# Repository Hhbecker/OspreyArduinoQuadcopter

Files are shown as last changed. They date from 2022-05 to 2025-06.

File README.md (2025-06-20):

<h1 align="center">
The Osprey Drone Mark I with Osprey Flight Controller Version 1.0
</h1>

<p align="center">
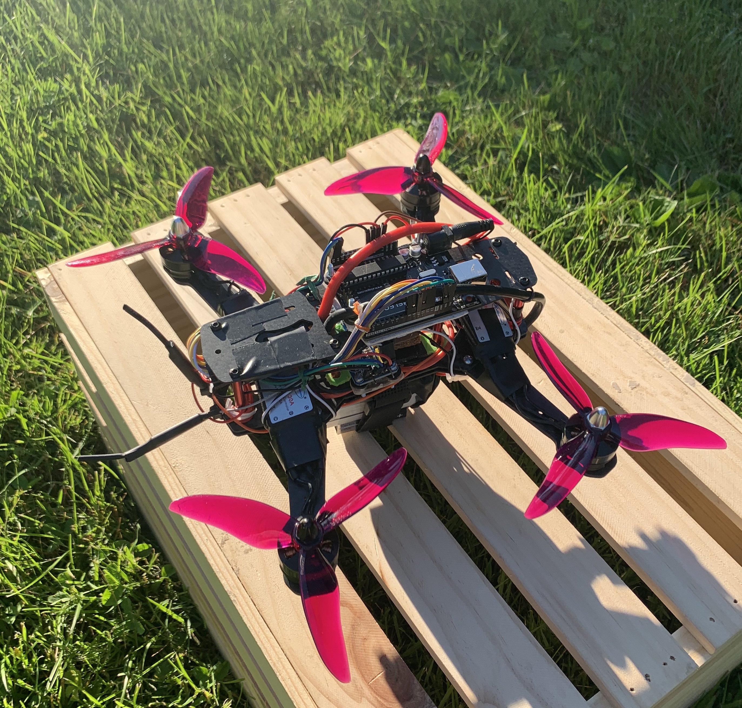
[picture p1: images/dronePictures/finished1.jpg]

</p>

<h5 align="center">
An Arduino based quadcopter build with personally developed flight control software
</h5>

### Features:
* Automated PID stabilization for roll pitch and yaw axes 
* Joystick control of roll pitch and yaw axes 
* Joystick throttle mapped directly to motor power
* Approximately 20Hz flight controller refresh rate

### Why Drones?
I see drones as the perfect engineering challenge because they require knowledge from a range of disciplines including physics, electrical engineering, computer science, and math. 
This drone project has also provided me with experience 1. developing embedded software for a real-time application, 2. designing and constructing circuits and electrical hardware, and 3. implementing an algorithm based on control theory mathematics. Not only are drones a great engineering challenge but they also have innumerous real world applications including in disaster relief, law enforcement, agriculture, and war. 

### Circuit Diagram
<p align="center">

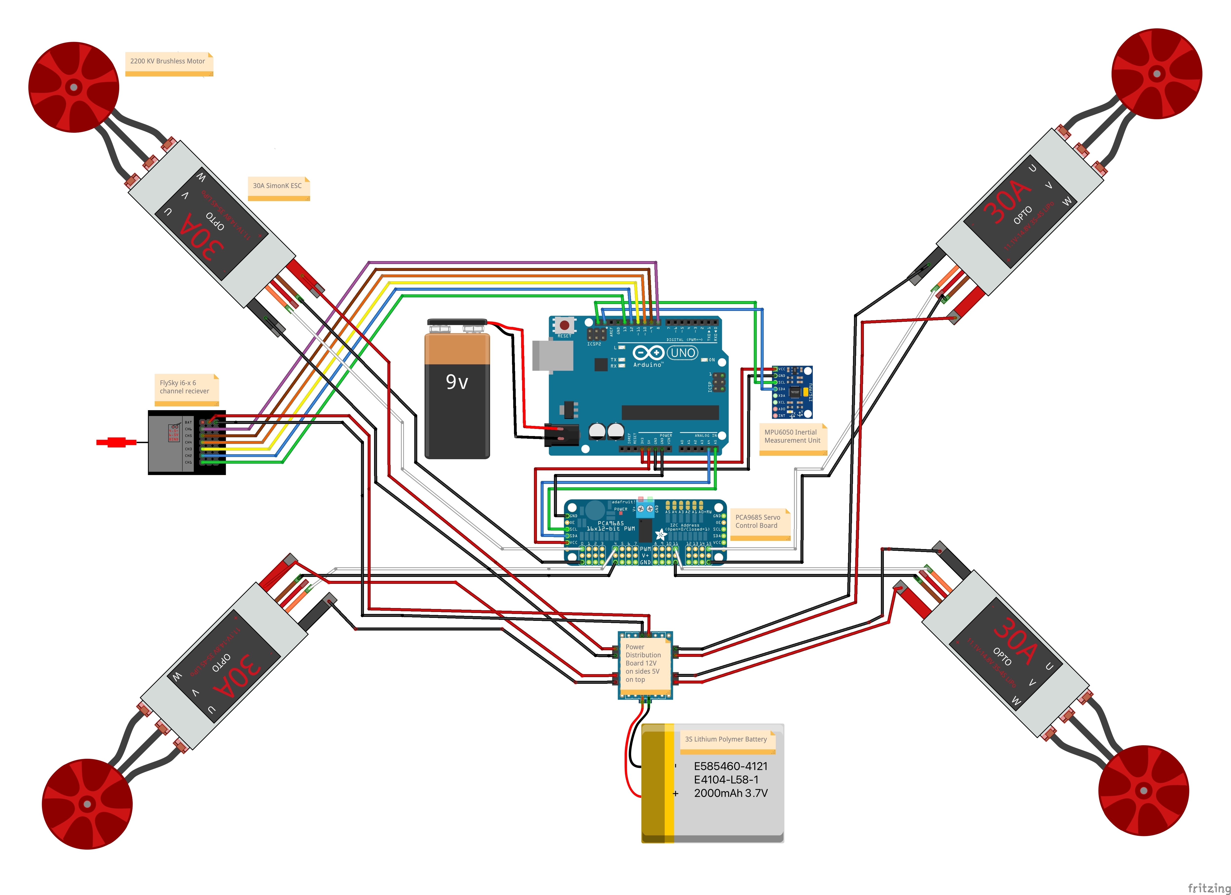
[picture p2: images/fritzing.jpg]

</p>

### The Basics of Quadcopter Flight
A drone has three axes of rotation: roll, pitch, and yaw. The primary goal of the Osprey Flight Controller V1.0 is to maintain stability in flight by continously adjusting the speed of each individual motor in order to abruptly and accurately correct any unwanted rotation about each of the three axes. The different colored rotors in the image below represent the front and rear rotors of the drone. It is important to mention that diagonal rotors spin in the same direction whereas adjacent motors spin in the opposite direction in order to balance the motor torques.

<p align="center">
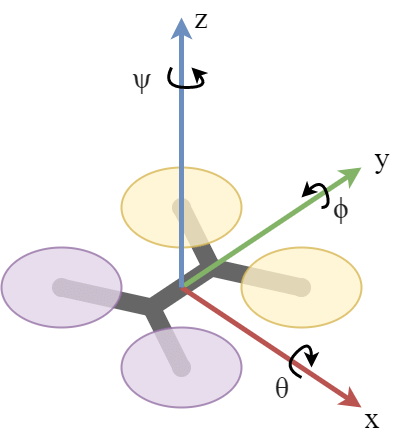
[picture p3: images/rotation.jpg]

</p>

<p align="center">
<b>Vizualization of the three axes of rotation. Y = roll, X = pitch, and Z = yaw.</b>
</p>

The onboard accelerometer and gyroscope are used to calculate the rotation of the drone along these three axes in real time. The observed rotation is fed into the flight control algorithm to calculate the new motor speeds necessary to correct for any unwanted rotation. The flight control algorithm runs in a loop continously making these corrections and adjustments throughout the duration of the flight. The stability of the drone is ultimately a function of how quickly corrections are calculated and implemented by the motors. Each component on the drone plays a role in accomplishing this task.

### Software Architecture 
The arduino runs a continuous loop with the same set of functions called each time the loop executes. The diagram below shows the main loop functions in the order of their execution. This code is pulled directly from the main loop of the Osprey Flight Controller V1.0.

<p align="center">
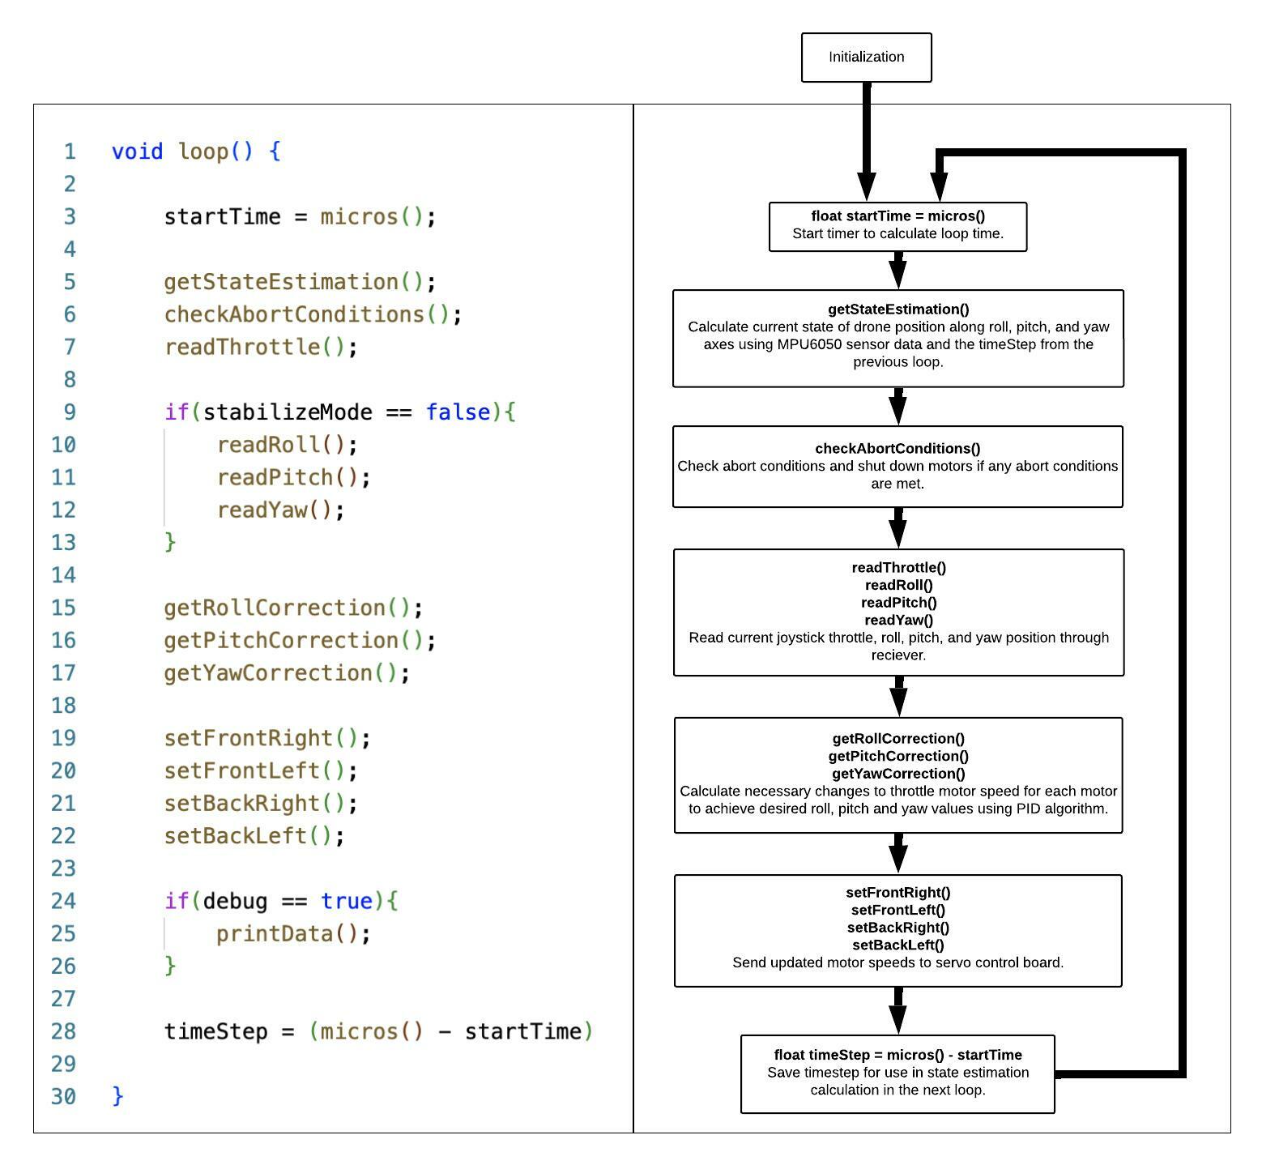
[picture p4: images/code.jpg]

</p>

### The Control Algorithm
Control theory is a branch of applied mathematics that deals with the use of feedback to influence the behaviour of a system in order to achieve a desired goal. In the case of drone flight, the current rotation about each axis must be "fed-back" into the control algorithm and used to determine how much the motor speeds should change to achieve the desired rotation set by the joysticks.

The method of feedback control used in the Osprey Flight Controller is known as PID Control. PID control is one of the most common control algorithms used in industry because it is simple to understand and implement yet still provides robust performance. PID algorithms consist of three basic coefficients; proportional, integral and derivative. These coefficients are scaled or "tuned" to get the optimal response. 

To better understand PID control let's use the roll axis of the Osprey drone as an example. As previously discussed, the flight controller calculates the drone's attitude about the roll axis and compares the current rotation to the desired rotation set by the joystick. Let's say the desired roll is 0º, but a gust of wind induces a roll of 30º. The error term (the difference between the current and desired rotation) is now 30º.

<p align="center">
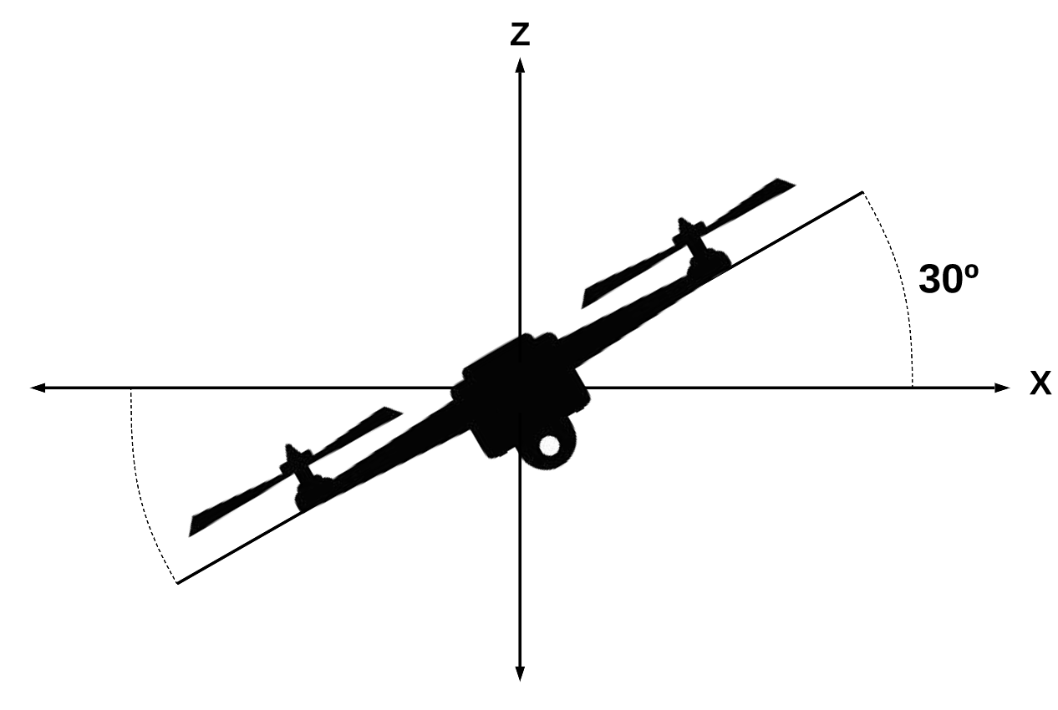
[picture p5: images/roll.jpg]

</p>

<p align="center">
<b>Drone rolling 30º with a setpoint of 0º resulting in a roll error term of 30.</b>
</p>

This error term is then passed into the PID controller. Inside the PID controller a proportional, integral, and derivative response to this error term are calculated separately and finally summed together. The sum of the proportional, integral, and derivative response to the error term is the output of the controller which is combined with the throttle value to calculate the new motor speeds. Notice the gain term (Kp for proportional, Ki for integral, and Kd for derivative) in front of each PID path in the diagram below. This gain is adjusted to increase or decrease the effect of the given term on the overall controller output. The PID tuning process is necessary to find the optimal response and robustness for a particular system. 

<p align="center">
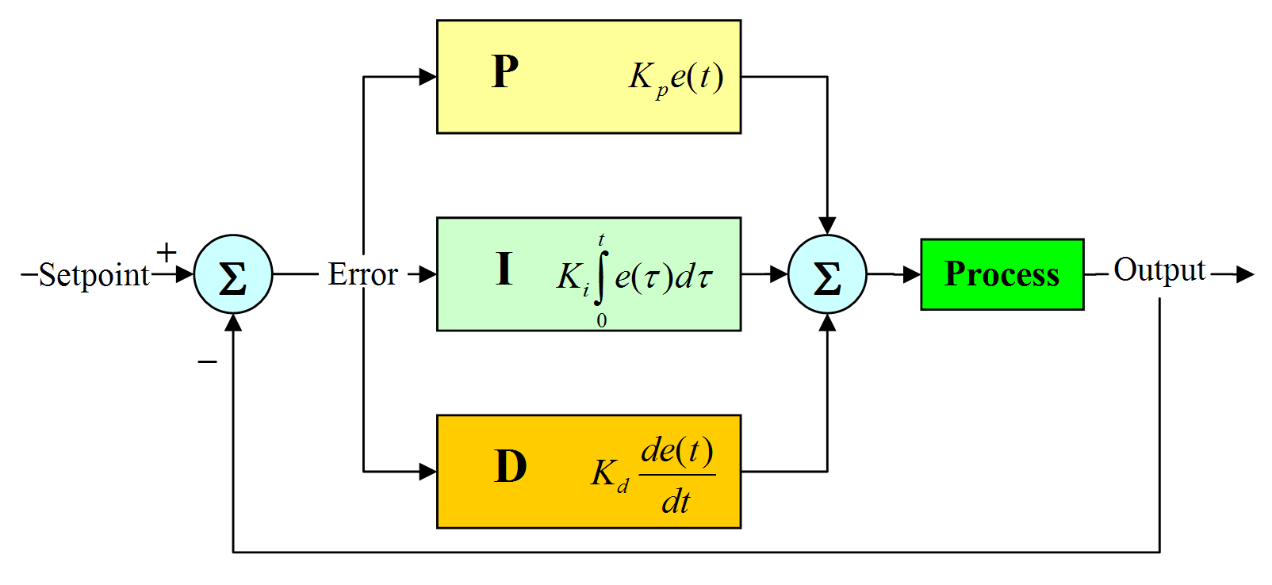
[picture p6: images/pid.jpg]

</p>

<p align="center">
<b>The structure of a PID controller showing the error term passed through the proportional, integral, and derivative paths.</b>
</p>

Because the drone is rolling to the left in our example we would expect our PID controller to reduce the power to the motors on the right and increase the power to the motors on the left. How do the proportional, integral, and derivative terms each respond to the error to affect the controller output?

#### Proportional term
As you might expect, the proportional term grows proportionally with the size of the error term. A larger error will result in a larger absolute contribution from the proportional term to the controller output. 

#### Integral term
The integral term is the integration of the error over time. With every execution of the loop, the current error is added to the sum of all past errors. The integral term is necessary to overcome what is known as steady state error. Steady state error occurs when an equilibrium is reached with the proportional term and an opposing force at a state of nonzero error. This often happens when the error term is small, because the proportional term will also be small and may be too small to compensate for the error. The integral term accumulates this residual error over time to drive the system toward its commanded value. Integral terms are tuned to be inconsequential in the transient response  and only become significant over time. Integral windup occurs when the integral term saturates the motor's capabilities and must be considered when designing a PID controller. A simple strategy to avoid integral windup is to cap the integral term at a predetermined value.

#### Derivative term
The derivative term takes into account the rate of change of the error term. The derivative term is sometimes called the damping term because its primary responsibility is to prevent the system from overcorrecting due to the contribution of the proportional term. The derivative term is constrained by its tendency to amplify sensor noise. If the derivative gain is too high, the system will lose stability because the derivative term's response to sensor noise  will exert an oversized affect on the controller output.

In summary, the basic idea behind a PID controller is to 1. Read a sensor, 2. Compute the difference between the sensor reading and the desired setpoint (the error term), and 3. Compute the desired change in motor power by summing a proportional, integral, and derivative response to the error term. 

#### PID Tuning
A flawless flight controller still will not fly without reasonable gains. Testing the overall function of the drone and tuning the gains in a safe and controlled environment before attempting to fly is the smart approach to drone development (I learned the hard way). To safely tune the gains I built a simple test rig shown below. The roll, pitch, and yaw axes must be tested and tuned individually. For each axis, the center of rotation on the test rig should be located directly through the center of gravity of the drone to best simulate flight. Make sure to balance weight, motor thrusts, and motor torques along each axis so the drone remains level on the test rig in the absence of perturbations before testing the PID controller.

<br/>

<p align="center">
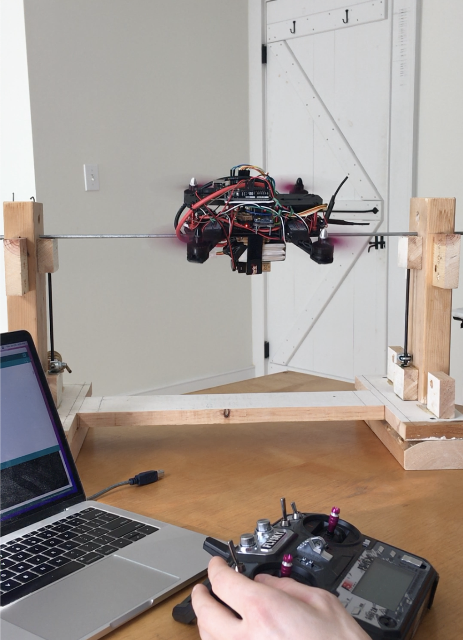
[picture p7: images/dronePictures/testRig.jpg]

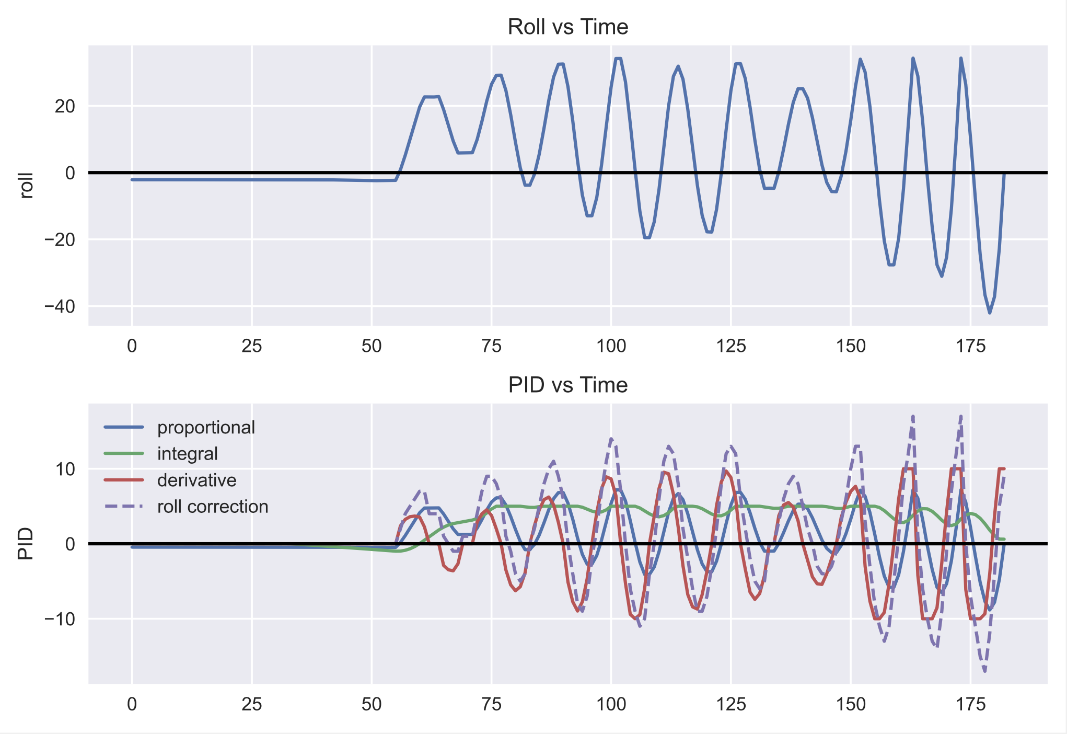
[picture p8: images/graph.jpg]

</p>

<p align="center">
<b>Left: handmade roll and pitch test rig. Right: graph of PID output during roll test.</b>
</p>

#### The Ziegler Nichols PID Tuning Method
1. Set integral and derivative gains to zero
2. Tune the proportional gain to achieve even, steady oscillations when perturbed. 
4. Add the derivative term and tune the gain to remove overshoot. 
5. Add the integral term and tune the gain to compensate for any steady state error.

### State Estimation 
The Osprey Flight Controller incorporates gyroscope and accelerometer data from the MPU6050 inertial measurement unit to achieve a 3 degrees of freedom attitude estimation about the roll, pitch, and yaw axes. The MPU6050 is a low budget, low power, 6-axis microelectromechanical inertial measurement unit that can easily interface with Arduino using the I2C protocol. 

<p align="center">
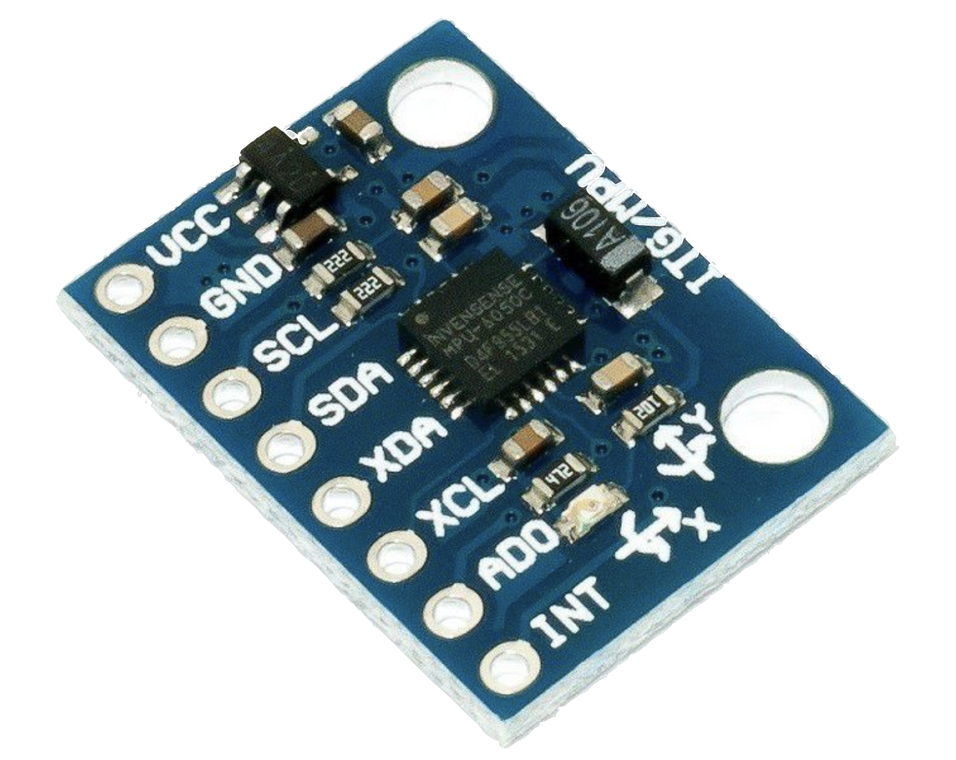
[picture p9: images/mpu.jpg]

</p>
<p align="center">
<b>An MPU6050 inertial measurement unit.</b>
</p>

The MPU6050 gyroscope measures angular rate. The angular rate is integrated with respect to time to get an estimate of the current position. Obviously, the smaller the timestep of the integration, the more accurate the angular position estimate will be. This method can be used to calculate roll, pitch, and yaw angular position estimates and is very accurate in flight. 

The MPU6050 accelerometer measures linear acceleration along the X, Y, and Z axes. The angular position is calculated from each accelerometer linear acceleration reading using Euler angle based trigonometry. Only roll and pitch can be calculated with this method. This calculation relies on the drone being in an inertial reference frame, where the accelerometer registers 1g. During accelerating flight, these calculations become inaccurate. At rest the accelerometer based estimations will recenter any gyroscope drift. Kornelius Jarzębski's MPU6050 library was used to calculate the accelerometer based angular position estimates and these estimates were fused with the gyroscope estimates using a low pass filter for the accelerometer based state estimation and a high pass filter for the gyroscope based state estimation. This filtering strategy is used because the accelerometer based estimations are susceptible to large amounts of error in the short term but do not drift in the long term, whereas the gyroscope based estimations are very accurate in the short term but will drift over time as small errors accumulate.

### Flight Controller Timing
Flight controller speed is crucial for drone stability. A slower flight controller loop time negatively affects stability because it decreases the accuracy of the state estimation and also does not give the motors as much time to adjust their speed. The Osprey Flight Controller relies on several different hardware components as well as software to do its job. It's important to understand the time it takes to complete each part of the loop, so that optimization efforts can focus on the biggest bottlenecks. The default operating frequency for Arduino Uno R3 is 16MHz. The average timestep (total loop time) of the Osprey Flight Controlller V1.0 is approximately 20Hz in Stabilize Mode. This is unfortunately far too slow to allow for the stability required to film or maneuver. Modern F4 flight controllers allow for incredibly smooth and aggresssive flight with loop times of 32KHz which is three orders of magnitude faster than the Osprey Flight Controller V1.0. 

The MPU6050 has a maximum sample rate north of 1Hz but in this project the MPU6050 is only sampled once every loop. The timestep is often kept constant when integrating sensor data with respect to time. I chose to vary the time step to avoid using the delay() function which is a blocking function and slowed the overall loop time too much. The best solution would be to handle integration of the sensor data on a separate microcontroller to allow for a constant timestep without slowing down other flight controller tasks. 

The internal clock of the servo control board can be set to operate at a frequency of up to 1526Hz. I set the frequency to 400Hz for communication with the SimonK ESCs. The SimonK ESCs are capabale of a 400Hz refresh rate. The motors are lower end but are still capable of accelerating and decellerating quickly enough.

### Construction Process
<p align="center">
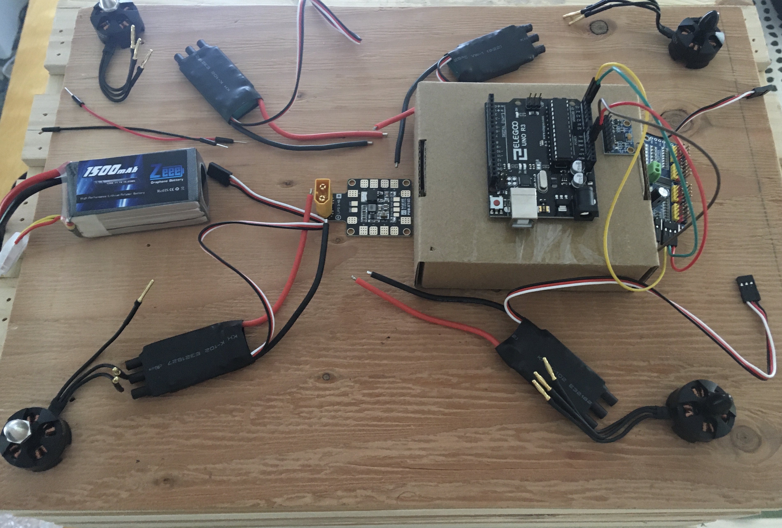
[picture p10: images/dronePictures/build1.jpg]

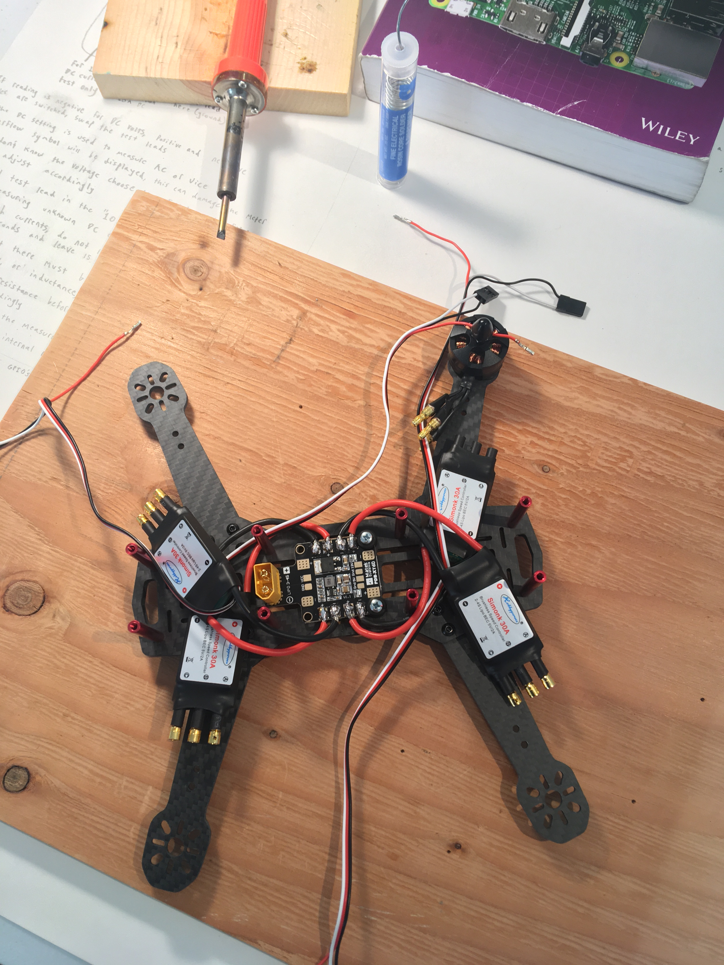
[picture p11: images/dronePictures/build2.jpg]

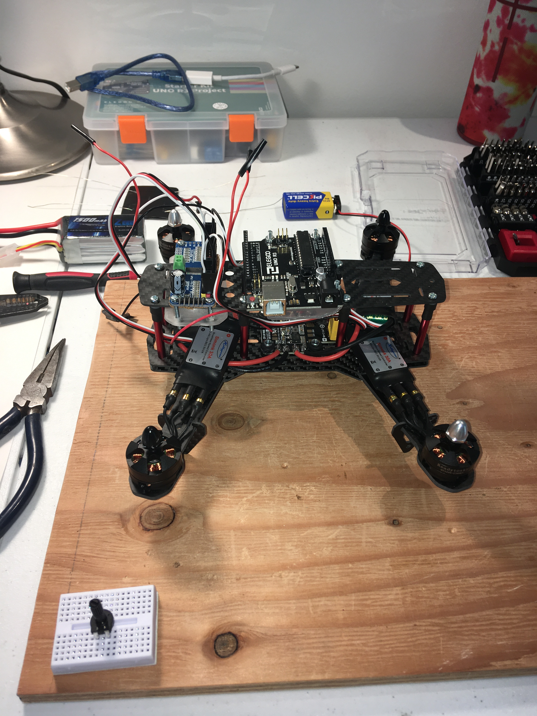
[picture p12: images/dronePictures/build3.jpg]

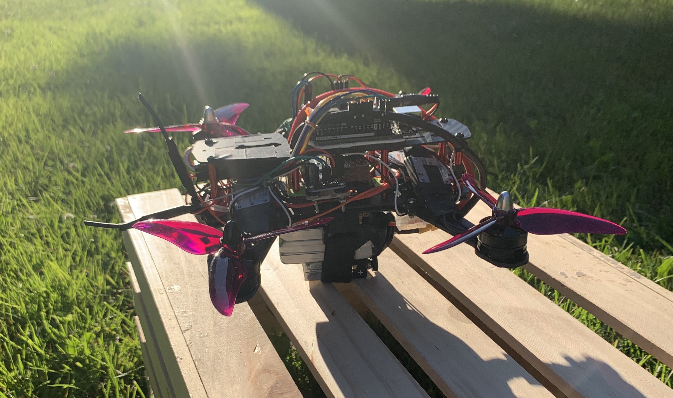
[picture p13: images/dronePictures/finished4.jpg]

</p>

</br>

<h3 align="center">
The Osprey Mark I in Action 
</h3>

<p align="center">

</p>

### Parts List
* Elegoo Uno R3 - x1
* HiLetgo MPU6050 - x1
* HiLetgo Servo Control Board PCA9685 - x1
* Matek Power Distribution Board 5V and 12V - x1
* Hobbypower SimonK 30A ESC - x4
* Readytosky 2300KV brushless DC motor - x4
* FlySky I6x Transmitter and Reciever - x1
* Zeee 11.1V 120C 1500mAh 3s Lithium Polymer Battery - x1
* Usmile 250mm carbon fiber FPV quadcopter frame - x1
* GEMFAN 5 inch propellor 3 blades - x1
* AstroAI Digital Multimeter - x1
* HTRC 2S-3S LiPo Balance Battery Charger - x1

### Next Steps

The Osprey Drone Mark I with the Osprey Flight Controller V1.0 marks my introduction to aerospace engineering generally and drones specifically. I was pleased with the result but there is much to improve on. 

**Software improvements:**
* Decrease flight controller refresh rate 
* Add altitude controller for hover
* Add translation controller to prevent wind drift 
* Represent state estimation using Quaternions instead of Euler Angles

**Hardware improvements:**
* Replace Arduino Uno with multiple Arduino Nanos
* Minimize length of all wires
* Design an outer shell to protect electrical components

<h4 align="center">
Thank you to Mom for the support, Dad for the support and the tools, and Conor for the inspo and advice!
</h4>

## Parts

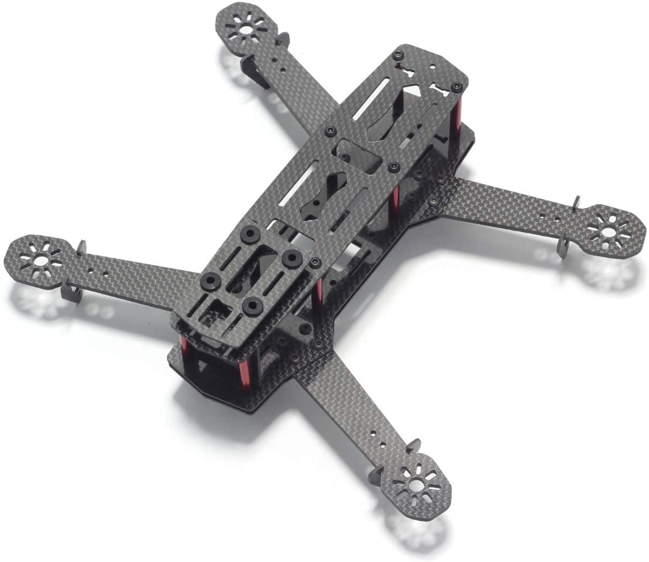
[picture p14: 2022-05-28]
images/parts/frame.jpg

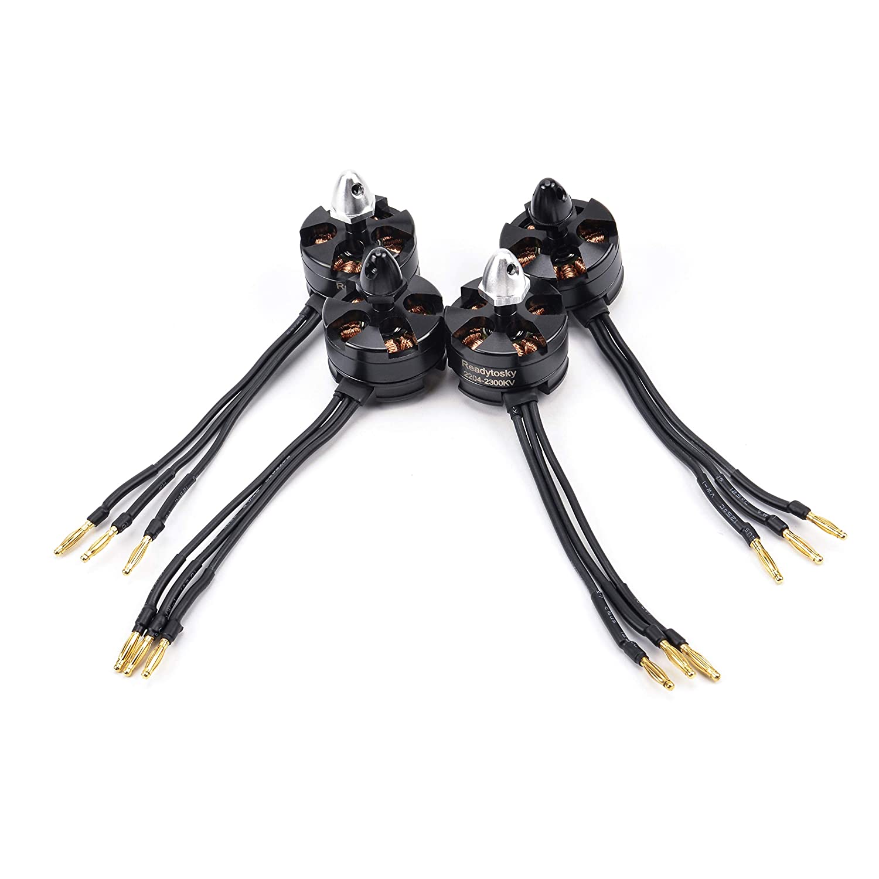
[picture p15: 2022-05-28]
images/parts/motors.jpg

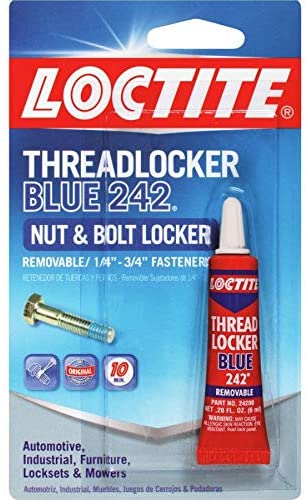
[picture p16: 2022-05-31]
images/parts/loctite.jpg

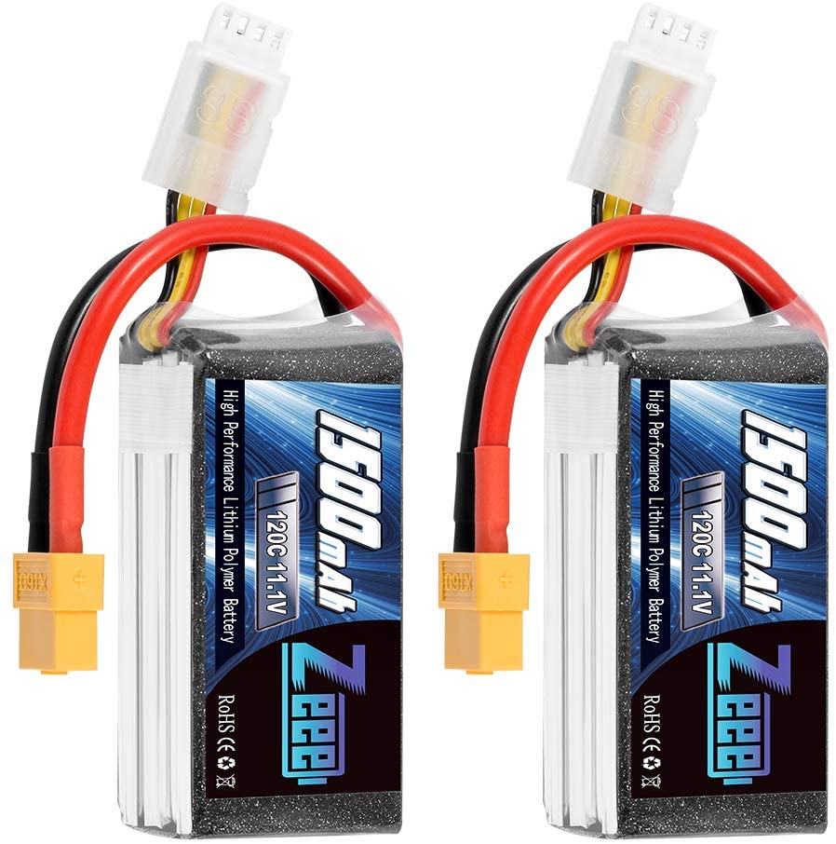
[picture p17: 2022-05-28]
images/parts/battery.jpg

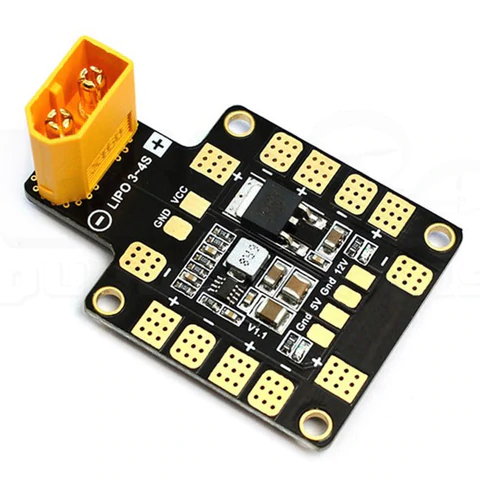
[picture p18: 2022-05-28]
images/parts/PDB.jpg

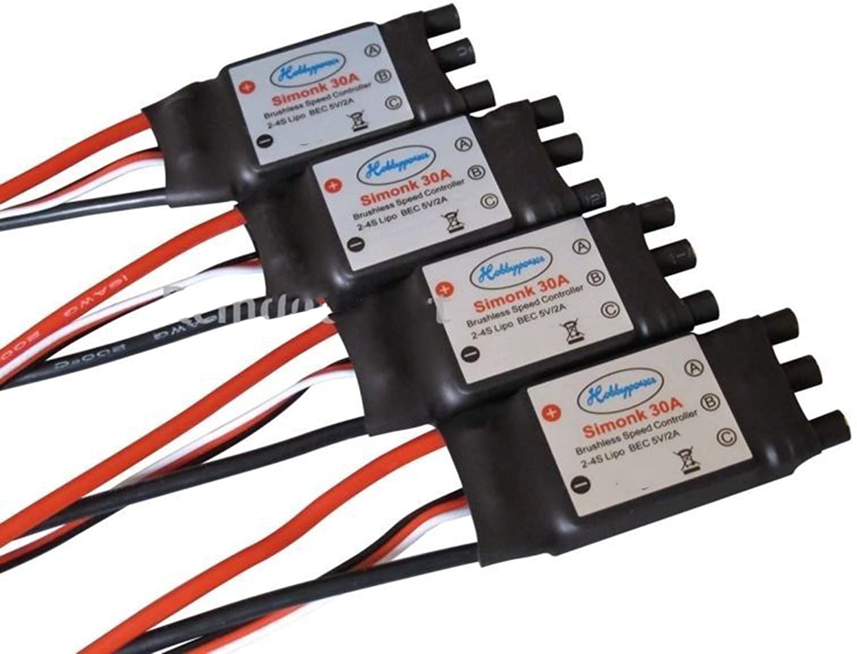
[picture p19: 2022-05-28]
images/parts/ESCs.jpg

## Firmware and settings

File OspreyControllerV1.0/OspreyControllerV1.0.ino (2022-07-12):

/*************************************************** 
Flight Controller for the Osprey Arduino Quadcopter

****************************************************/

/* 
 *  Important Remdiners
 *  -timestep initialized to zero meaning it's zero for the first call to getStateEstimation()
 *  -when reading pulse from arduino pins connected to reciever the policy is to set the reciever value to zero if the timeout is reached
 *  -currently no anti windup scheme or throttle minimum for i term
 */


#include <Wire.h>
#include <Adafruit_PWMServoDriver.h>
#include <math.h>
#include <MPU6050.h>
#include "functions.h"

bool debug = false; 
bool stabilizeMode = true;
bool abortSwitch = false;

float rollPgain = 0.04;
float rollIgain = 0.003; // 0.003 
float rollDgain = 0.06; // 0.06

float pitchPgain = 0.07;
float pitchIgain = 0.007; // 0.007
float pitchDgain = 0.06; // 0.07

float yawPgain = 0.02;
float yawIgain = 0.00;
float yawDgain = 0.03;

// CONTROLLER AND RECIEVER SETUP

int CH1 = 13; // roll (aileron)
int CH2 = 12; // pitch (elevator)
int CH3 = 11; // throttle
int CH4 = 10; // yaw (rudder)
int CH5 = 9; // abort switch
int CH6 = 8; // unused switch

//Floating point math is also much slower than integer math in performing calculations, 
//so should be avoided if, for example, a loop has to run at top speed for a critical 
//timing function. Programmers often go to some lengths to convert floating point 
//calculations to integer math to increase speed.

//C++ always truncates aka rounds down to the nearest integer equal to or less than the floating point value.

int ch1Value;
int ch2Value;
int ch3Value;
int ch4Value;
int ch5Value;
unsigned long timeout = 30000; // 1,000,000 = 1 second


int throttle;
int frontRight;
int frontLeft;
int backRight;
int backLeft;

// roll only
float rollValue = 0.0f;
float rollError;
float rollProportional;
float rollIntegral = 0.0f;
float rollDerivative;
float rollCorrection = 0;

float pitchValue = 0.0f;
float pitchError;
float pitchProportional;
float pitchIntegral = 0.0f;
float pitchDerivative;
float pitchCorrection;

float yawValue = 0.0f;
float yawError;
float yawProportional;
float yawDerivative;
float yawCorrection;

// SERVO BOARD SETUP
// called this way, it uses the default address 0x40
Adafruit_PWMServoDriver pwm = Adafruit_PWMServoDriver();

int SERVOMIN = 215; // minimum pulse length count (out of 4096) the ESC will recognize
int SERVOMAX = 300; // maximum pulse length count (out of 4096) the ESC will recognize // FLIGHT = 400 ROLL TEST = 350

int JOYSTICKMIN = -15;
int JOYSTICKMAX = 15;

// MPU6050 SETUP
// Because of the mounting orientation of the chip on the drone: 
// PITCH = X axis
// ROLL = y axis

MPU6050 mpu;

// Timers
unsigned long timer = 0;
float timeStep = 0.0;

// Pitch, Roll and Yaw values
float gyroPitch;
float gyroRoll;
float gyroYaw;
float accelPitch;
float pitchOffset;
float accelRoll;
float rollOffset;
float pitch;
float roll;

Vector normGyro;
Vector normAccel;



/////////////////////////////////////////////////// SETUP FUNCTION 

void setup() {

    if(debug == true){
        Serial.begin(115200);
    }

    initializeRecieverPins();

    initializeServoBoard();

    initializeIMU();

    setAccelerometerOffset();

}

/////////////////////////////////////////////////// LOOP FUNCTION 


void loop() {

    // timer for gyroscope timestep
    // returns the number of milliseconds passed since the arduino board began running the current program
    timer = micros();

    getStateEstimation();
    checkAbortConditions();
    readThrottle();

    if(stabilizeMode == false){
        readRoll();
        readPitch();
        readYaw();
    }

    getRollCorrection();
    getPitchCorrection();
    getYawCorrection();
   
    setFrontRight();
    setFrontLeft();
    setBackRight();
    setBackLeft();
    
    
    if(debug == true){
        printData();
    }
    
    timeStep = (float) (micros() - timer)/1000000;

    
}

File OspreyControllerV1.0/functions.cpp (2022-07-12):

/*************************************************** 
Flight controller functions
July 2022
Henry Becker
****************************************************/



#include "functions.h"

/////////////////////////////////////////////////// CUSTOM FUNCTIONS /


    // Establish arduino pins to recieve signals from reciever
    void initializeRecieverPins(){
        // CONTROLLER AND RECIEVER SETUP
        pinMode(CH1, INPUT); // roll (aileron)
        pinMode(CH2, INPUT); // pitch (elevator)
        pinMode(CH3, INPUT); // throttle
        pinMode(CH4, INPUT); // yaw (rudder)
        pinMode(CH5, INPUT); // abort switch
        pinMode(CH6, INPUT); // unused switch
    }


    // Set internal clock of servo board for pwm communication with SimonK hobbypower ESCs
    void initializeServoBoard(){
        // SERVO BOARD SETUP
        // The internal oscillator (clock) for the PCA9685 chip is in a range between about 23-27MHz 
        pwm.begin();
        pwm.setOscillatorFrequency(27000000); // 27 MHz
        pwm.setPWMFreq(400);  // Analog servoes run at ~50 Hz updates but we aren't communicating directly with the motor we're communicating with an esc that operates at max of 400hz 
    }


    // Initialize and calibrate mpu6050 sensor
    void initializeIMU(){
        // MPU6050 SETUP
        while(!mpu.begin(MPU6050_SCALE_2000DPS, MPU6050_RANGE_2G))
        {
            if(debug == true){
                Serial.println("Could not find a valid MPU6050 sensor, check wiring!");
            }
            
            delay(100);
        }
    
        // Calibrate gyroscope. Calibration must be at rest.
        mpu.calibrateGyro();
        
        // Set threshold sensivty. Default 3.
        mpu.setThreshold(3);
    }


    // Use an average of 1000 accelerometer readings to set initial gyroscope reading
    void setAccelerometerOffset(){
        // The acceleromter is used to calculate angular position using trigonometry based on the known vector of gravity with an acceleration of 1g downward
        // The position calculated using the accelerometer is then given as the starting point for the gyrsocope
        
        rollOffset = 0.0;
        pitchOffset = 0.0;

        // average 1000 accelerometer readings for a more accurate offset
        for(int i=0; i<1000; i++){
            
            normAccel = mpu.readNormalizeAccel();
            rollOffset = rollOffset + (-(atan2(normAccel.XAxis, sqrt(normAccel.YAxis*normAccel.YAxis + normAccel.ZAxis*normAccel.ZAxis))*180.0)/M_PI);
            pitchOffset = pitchOffset + ( (atan2(normAccel.YAxis, normAccel.ZAxis)*180.0)/M_PI);
        }

        rollOffset = rollOffset/1000;
        pitchOffset = pitchOffset/1000;

        roll = rollOffset;
        pitch = pitchOffset;
        
    }


    // Convert MPU6050 gyroscope and accelerometer readings into accurate attitude estimation 
    void getStateEstimation(){
        // GYRO DATA
        // Read normalized values
        normGyro = mpu.readNormalizeGyro();
    
        // Iintegrate gyroscope data
        gyroRoll = roll + (normGyro.YAxis * timeStep);    // switched gryoRoll for roll
        gyroPitch = pitch + (normGyro.XAxis * timeStep);  // switched gyroPitch for pitch
        gyroYaw = gyroYaw + (normGyro.ZAxis * timeStep);
    
        // ACCELEROMETER DATA
        // Read normalized values 
        normAccel = mpu.readNormalizeAccel();
    
        // Calculate Roll and Pitch from accelerometer readings using Euler angles
        accelRoll = -(atan2(normAccel.XAxis, sqrt(normAccel.YAxis*normAccel.YAxis + normAccel.ZAxis*normAccel.ZAxis))*180.0)/M_PI;

        accelPitch = (atan2(normAccel.YAxis, normAccel.ZAxis)*180.0)/M_PI;
    
        // Sensor fusion using COMPLIMENTARY FILTER
        pitch = (0.995*gyroPitch) + (0.005*accelPitch);
        roll = (0.995*gyroRoll) + (0.005*accelRoll);
        
    }


    // Constrain receiver value to range 1000-2000 (sometiems reciever will read values slightly above or below 1000-2000)
    int mapReceiver(int input){
        
        if(input > 2000){
            return 2000;
        }
        else if(input < 1000){
            return 1000;
        }
        else {
            return input;
        }
    }

    // Map thorttle joystick value to be compatible with the SERVOMIN and SERVOMAX values used in setPWM function
    void readThrottle(){
        
        // read pulse from receiver channel 3 (throttle stick) and map it to range 1000-2000
        int pulse = pulseIn(CH3, HIGH, timeout);

        if(pulse == 0){
            return;
        }
        
        throttle = mapReceiver(pulse);
        
        // map receiver input value range of 0-1023 to a value range of 0-180 which the ESC understands 
        throttle = map(throttle, 1000, 2000, SERVOMIN, SERVOMAX);
        
    }

    // Read desired roll angle from joystick
    void readRoll(){
        
        // read pulse from receiver channel 3 (throttle stick) and map it to range 1000-2000
        int pulse = pulseIn(CH1, HIGH, timeout);

        if(pulse == 0){
            return;
        }
        
        rollValue = mapReceiver(pulse);
        
        // map receiver input value range of 0-1023 to a value range of 0-180 which the ESC understands 
        rollValue = map(rollValue, 1000, 2000, JOYSTICKMIN, JOYSTICKMAX);
        
    }


    // Read desired pitch angle from joystick
    void readPitch(){
        
        // read pulse from receiver channel 3 (throttle stick) and map it to range 1000-2000
        int pulse = pulseIn(CH2, HIGH, timeout);

        if(pulse == 0){
            return;
        }
        
        pitchValue = mapReceiver(pulse);
        
        // map receiver input value range of 0-1023 to a value range of 0-180 which the ESC understands 
        pitchValue = map(pitchValue, 1000, 2000, JOYSTICKMIN, JOYSTICKMAX);
        
    }


    // Read desired yaw angle from joystick
    void readYaw(){
        
        // read pulse from receiver channel 3 (throttle stick) and map it to range 1000-2000
        int pulse = pulseIn(CH1, HIGH, timeout);

        if(pulse == 0){
            return;
        }
        
        yawValue = mapReceiver(pulse);
        
        // map receiver input value range of 0-1023 to a value range of 0-180 which the ESC understands 
        yawValue = map(yawValue, 1000, 2000, JOYSTICKMIN, JOYSTICKMAX);
        
    }

    // Turn off motors if abort conditions are met
    void checkAbortConditions(){

        // if pitch or roll exceeds 80º
        if(abs(pitch) > 80 || abs(roll) > 80){
            killMotors();
        }
        
        // Abort switch on RC controller
        if(pulseIn(CH5, HIGH, timeout) > 1500){
            killMotors();
        }
        
    }


    // Turn off motors
    void killMotors(){
        
        pwm.setPWM(0, 0, SERVOMIN);
        pwm.setPWM(1, 0, SERVOMIN);
        pwm.setPWM(14, 0, SERVOMIN);
        pwm.setPWM(15, 0, SERVOMIN);
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

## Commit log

2022-05-28 removed servo board notes
2022-05-29 tuning PID gains
2022-06-04 PID roll test draft 1
2022-06-27 roll, pitch, yaw PID complete
2022-07-12 added fritzing diagram
    [OspreyDroneMarkI.fzz]
2022-07-13 gif change
    [OspreyDroneMarkI.fzz]
